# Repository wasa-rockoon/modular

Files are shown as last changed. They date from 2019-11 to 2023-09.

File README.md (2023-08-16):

# モジュラー電装

# バス

バスの物理規格は，2.54mmピッチのカードエッジコネクタとする．片面15ピンずつ．

CANを用いた通信プロトコルは [WCCP](https://github.com/wasa-rockoon/WCCP)を参照．

表
1. Vpp
2. Vcc 5V
3. Vdd 3.3V
4. VBAT 3V
5. GND
6. CAN Low
7. CAN High
8. GND
9. キー
10. JTMS, SWDIO
11. JTCK, SWCLK
12. JTDI
13. JTDO, TRACESWO
14. /JNTRST
15. /RESET
裏

16 ~ 23, 25 ~ 30. テスト用プローブ 1 ~ 8, 9 ~ 14

24. キー

## Vpp, Vcc, Vdd, GND

電源モジュールから供給される．バスからのVpp供給は小電流に限る．大電流が必要なモジュールには電源モジュールまたは外部から直接供給すること．

## CAN High, CAN Low

5V CANバス, Normal CAN 1Mbps

## SWCLK, SWDIO, RST

STM32書き込み・デバッグ用

# モジュール一覧

## ベース基板

6個のモジュールを搭載できるベース基板．
カードエッジコネクタのうち1つを書き込み・デバッグ用とする．

- カードエッジコネクタ x6
- CANバスコネクタ x2
- STLink 書き込み・デバッグ用コネクタ x1
- テスト用カードエッジ

### CANバスコネクタ

ベース基板に取り付けないモジュールとの中距離接続に用いる．

1. Vpp
2. CAN Low
3. CAN High
4. GND

Vcc, Vddはモジュール側で自給する．

接続しない場合は，CAN Low と CAN High との間に終端抵抗（120 Ω）を必ず接続すること．

## Battery Power

- 5Vおよび3.3Vの電源を供給
- 各系統の電圧および電流を測定

### 接続

- 電源供給（6V~18V）：XH (1: V+, 2: GND)

### インターフェース

- 主電源スイッチ
- バックアップ電源スイッチ

### 出力パケット

#### B （Battery）

| Type | Data | Description |
| --- | --- | --- |
| P | float16 | 供給電源電圧 [V] |
| C | float16 | 5V系電圧 [V] |
| D | float16 | 3.3V系電圧 [V] |
| c | float16 | 5V系電圧 [A] |
| d | float16 | 3.3V系電流 [A] |

## Battery Power V2

- 5Vおよび3.3Vの電源を供給
- 各系統の電圧および電流を測定
- 外部に5Vまたは3.3Vの電源を供給
- バッテリー温度を測定し，ヒーターを駆動

### 接続

- 電源供給1（6V~18V）：XH (1: V+, 2: GND)
- 電源供給2（6V~18V）：XH (1: V+, 2: GND)
- ヒーター：PH (1: Heater+, 2: GND, 3: temperature)
- 外部供給出力（5V or 3.3V）：PH (1: V+, 2: GND, 3: flight pin)
- 外部電源スイッチ：PH

### インターフェース

- 5V・3.3V系電源スイッチ（外部スイッチとどちらかがONならば供給）

### 出力パケット

#### B （Battery）

| Type | Data | Description |
| --- | --- | --- |
| P | float16 | 供給電源電圧 [V] |
| C | float16 | 5V系電圧 [V] |
| D | float16 | 3.3V系電圧 [V] |
| c | float16 | 5V系電圧 [A] |
| d | float16 | 3.3V系電流 [A] |

## Comm&Log

- LoRa（ES920LR）通信
- TWELITE 通信
- Micro SD カードにログを記録

### 接続

- LoRa アンテナ：U.FL
- TWELITE アンテナ：U.FL

### インターフェース

- Micro SD カードスロット

## LoRa

- LoRa（ES920LR）通信（2ch）

### 接続

- LoRa アンテナx2：U.FL

## Igniter Driver

- 発射条件を判定しイグナイタを駆動
- 供給電圧，電流，イグナイタ抵抗値を測定

### 接続

- イグナイタ用供給（6V~12V）：XH (1: V+, 2: GND)
- イグナイタ出力：XH (1: V+, 2: GND)

### インターフェース

- 警報ブザー

## Nav

- 9軸センサ（BMX055）
- 気圧センサ（BME280）
- GNSS

### 接続

- GPS パッシブアンテナ：U.FL
- UART （外部GPS用）：PH
- I2C （拡張用）：PH

## INS

- 9軸センサ（BNO055）
- 気圧センサ（BME280）
- GNSS (NEO-M9N-00B)

### 接続

- GPS アクティブアンテナ：U.FL
- サーミスタ：PH
- UART （拡張用）：PH
- I2C （拡張用）：PH

## RCS

- 電磁バルブ制御x4
- バルブ用電源（24V）供給
- 圧力計測（1MPaG）x2
- 推力計測x2
- 温度計測

### 接続

- バルブAB：PH (1: A+, 2: A-, 3: B+, 4: B-)
- バルブCD：PH (1: C+, 2: C-, 3: D+, 4: D-)
- ロードセルX：ZH (1: Vdd, 2: GND, 3: Signal+, 4: Signal-)
- ロードセルY：ZH (1: Vdd, 2: GND, 3: Signal+, 4: Signal-)
- 圧力センサ1：ZH (1: Vcc, 2: GND, 3: Signal)
- 圧力センサ2：ZH (1: Vcc, 2: GND, 3: Signal)
- サーミスタ：ZH

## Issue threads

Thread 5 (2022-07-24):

位置情報表示器

fujiy, 2022-07-24:
地上局で位置情報を表示するものが欲しい
2個あるといいかも

https://paper.dropbox.com/doc/--Bk29owoF~U5IUNhlMDIlKGDbAQ-byOXNlpulk8jaebLoAD3U

- [x] ブレッドボードモデル製作
- [x] プログラム製作
- [x] 本番用基板製作

Closed 2023-04-29.

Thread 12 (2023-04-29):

点火モジュール改良

fujiy, 2023-04-29:
基板作り直すなら
- MOSFETの定格増やす
- 電流測定回路間違ってたので修正する
- 温度センサ付けられるようにする

fujiy, 2023-07-29:
去年のモジュールを使うが，電流をコントロールするようにプログラムを改良する

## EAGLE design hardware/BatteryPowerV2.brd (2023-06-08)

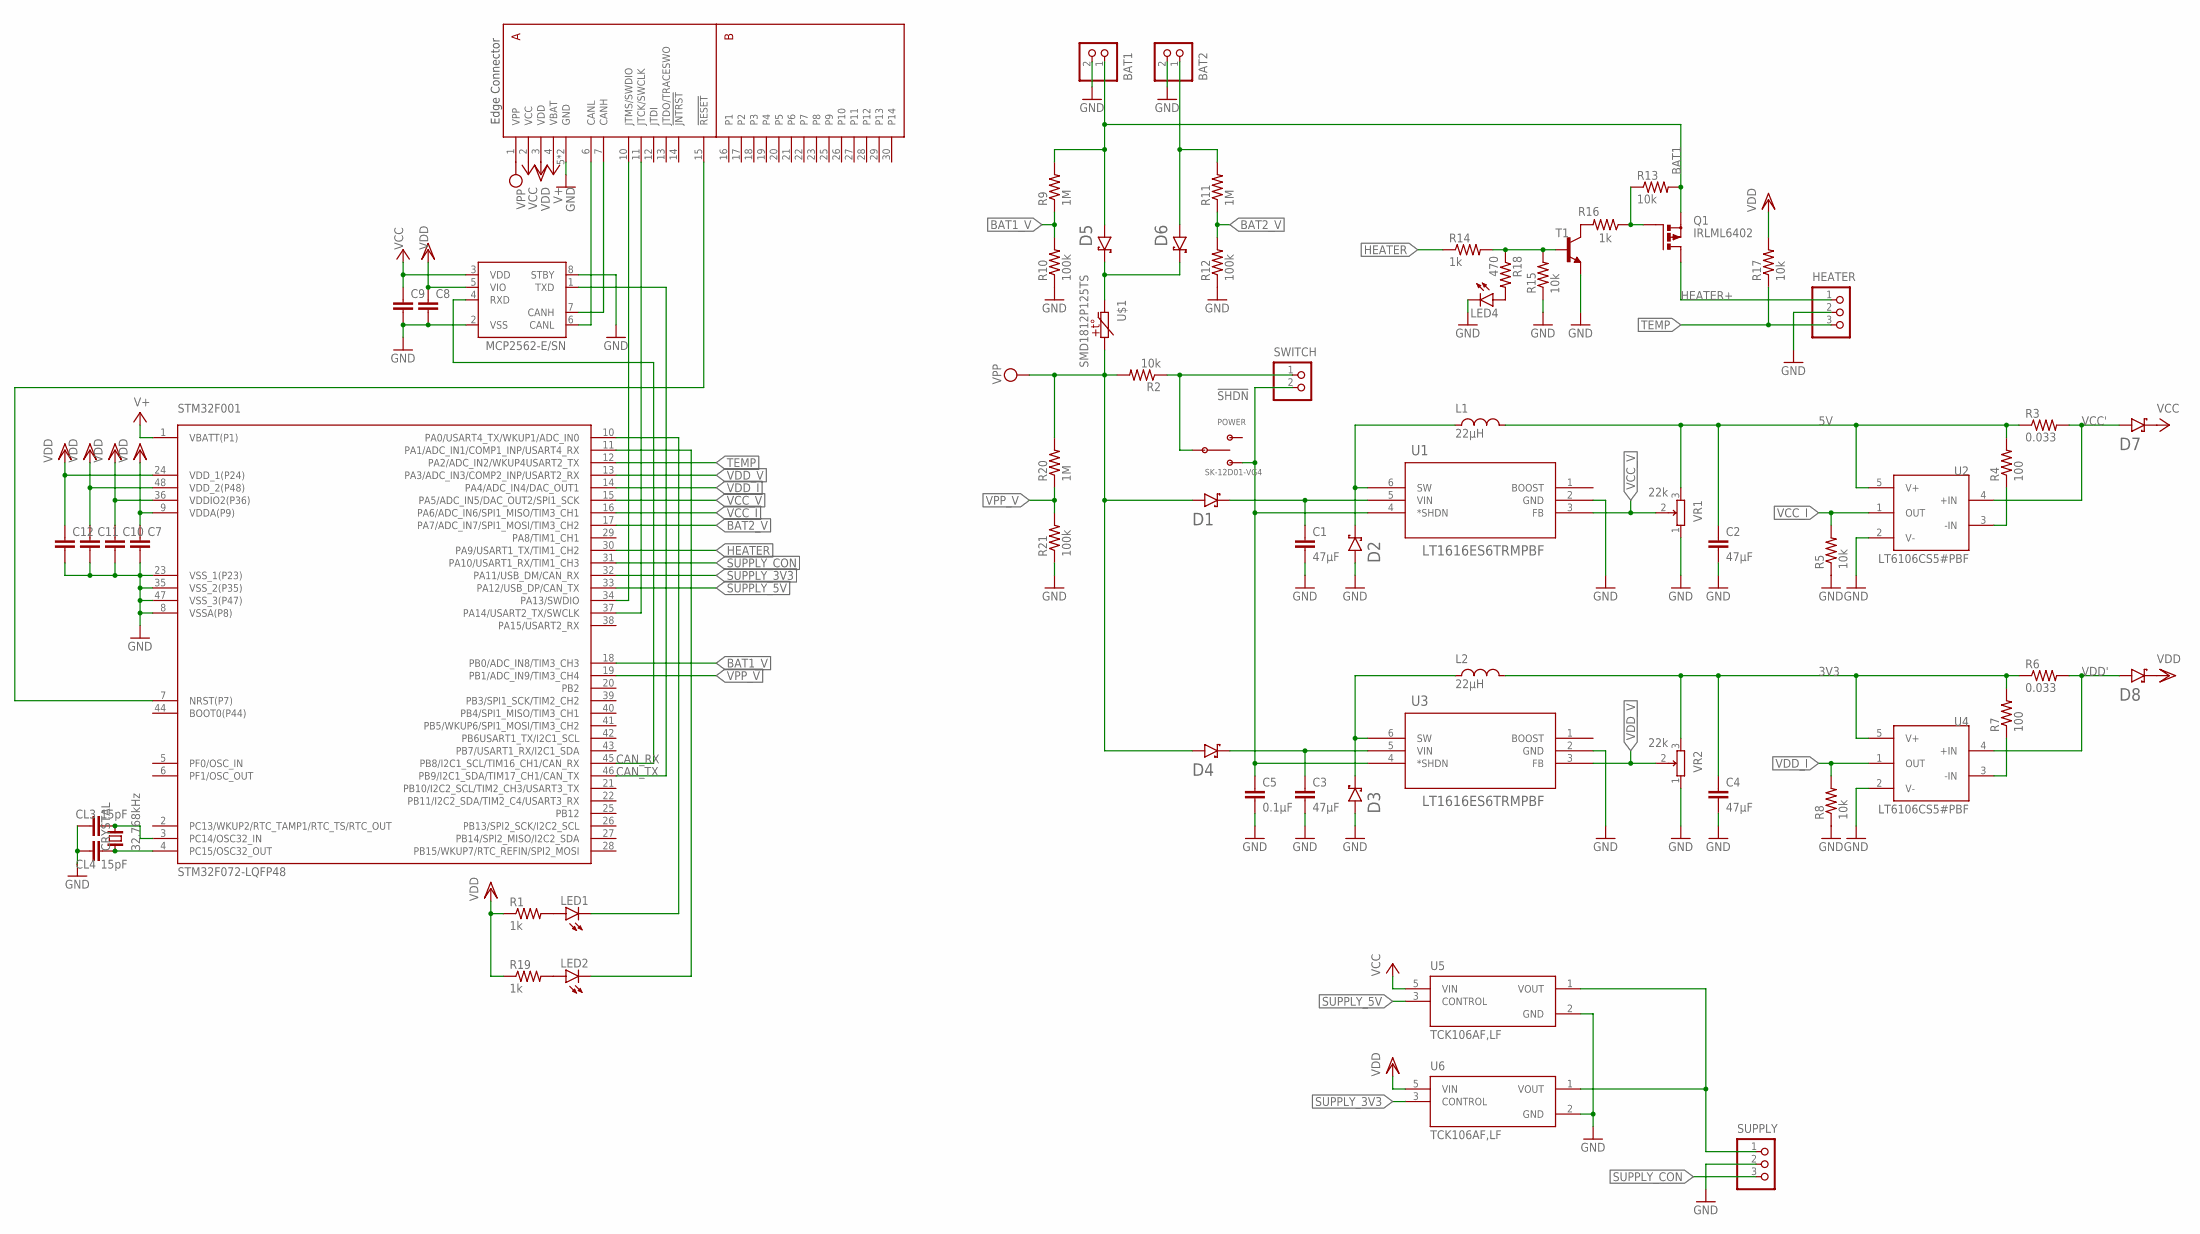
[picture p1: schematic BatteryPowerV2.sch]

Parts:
BAT1, BAT2: S2B-XH-A
C1, C2, C3, C4: 47µF; C0603
C5: 0.1µF; C0603
C7, C8, C9, C10, C11, C12: C-EUC0603K; C0603K
CL3, CL4: 15pF; C0603K
CRYSTAL: 32.768kHz; FC-255
D1, D2, D3, D4, D5, D6, D7, D8: CUHS20S30
HEATER: S3B-PH-K-S
L1, L2: 22µH; NR10050
LED1, LED2: LEDCHIP-LED0603; CHIP-LED0603
LED4: LEDCHIPLED_0603; CHIPLED_0603
MCP2562: MCP2562-E/SN; SOIC127P600X175-8N
POWER: SK-12D01-VG4
Q1: IRLML6402; SOT-23
R1, R14, R16, R19: 1k; R0603
R2, R5, R8, R13, R15, R17: 10k; R0603
R3, R6: 0.033; R0603
R4, R7: 100; R0603
R9, R11, R20: 1M; R0603
R10, R12, R21: 100k; R0603
R18: 470; R0603
STM32F001: STM32F072-LQFP48; LQFP48
SUPPLY: S3B-PH-K-S
SWITCH: S2B-PH-K-S
T1: -NPN-SOT23-EBC; SOT23-EBC
U1, U3: LT1616ES6TRMPBF; SOT-6_S
U2, U4: LT6106CS5#PBF; SOT95P280X100-5N_LT6106CS5#PBF
U5, U6: TCK106AF,LF; IC_TCK106AF,LF
U$1: SMD1812P125TS; SMD1812P
U$2: EDGE30
VR1, VR2: 22k; PVZ3A

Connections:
3V3: C4.1, L2.2, R6.1, R7.2, U4.5 (V+), VR2.3
5V: C2.1, L1.2, R3.1, R4.2, U2.5 (V+), VR1.3
!SHDN!: C5.1, POWER.B, SWITCH.2, U1.4 (*SHDN), U3.4 (*SHDN)
BAT1: BAT1.1, D5.A, Q1.P2 (S), R9.2, R13.2
BAT1_V: R9.1, R10.2, STM32F001.18 (PB0/ADC_IN8/TIM3_CH3)
BAT2: BAT2.1, D6.A, R11.2
BAT2_V: R11.1, R12.2, STM32F001.17 (PA7/ADC_IN7/SPI1_MOSI/TIM3_CH2)
CANH1: MCP2562.7 (CANH), U$2.7 (CANH)
CANL1: MCP2562.6 (CANL), U$2.6 (CANL)
CAN_RX: MCP2562.4 (RXD), STM32F001.45 (PB8/I2C1_SCL/TIM16_CH1/CAN_RX)
CAN_TX: MCP2562.1 (TXD), STM32F001.46 (PB9/I2C1_SDA/TIM17_CH1/CAN_TX)
GND: BAT1.2, BAT2.2, C1.2, C2.2, C3.2, C4.2, C5.2, C7.2, C8.2, C9.2, C10.2, C11.2, C12.2, CL3.1, CL4.1, D2.A, D3.A, HEATER.2, LED4.C, MCP2562.2 (VSS), MCP2562.8 (STBY), R5.1, R8.1, R10.1, R12.1, R15.1, R21.1, STM32F001.8 (VSSA(P8)), STM32F001.23 (VSS_1(P23)), STM32F001.35 (VSS_2(P35)), STM32F001.47 (VSS_3(P47)), SUPPLY.2, T1.E, U1.2 (GND), U2.2 (V-), U3.2 (GND), U4.2 (V-), U5.2 (GND), U6.2 (GND), U$2.5 (GND), U$2.8 (GND), VR1.1, VR2.1
HEATER: R14.1, STM32F001.30 (PA9/USART1_TX/TIM1_CH2)
HEATER+: HEATER.1, Q1.P3 (D)
unnamed: SUPPLY.1, U5.1 (VOUT), U6.1 (VOUT)
unnamed: R4.1, U2.3 (-IN)
unnamed: Q1.P1 (G), R13.1, R16.1
unnamed: LED2.C, STM32F001.11 (PA1/ADC_IN1/COMP1_INP/USART4_RX)
unnamed: R7.1, U4.3 (-IN)
unnamed: POWER.C, R2.1, SWITCH.1
unnamed: LED2.A, R19.2
unnamed: R14.2, R15.2, R18.1, T1.B
unnamed: R16.2, T1.C
unnamed: LED4.A, R18.2
unnamed: CL4.2, CRYSTAL.1, STM32F001.4 (PC15/OSC32_OUT)
unnamed: CL3.2, CRYSTAL.2, STM32F001.3 (PC14/OSC32_IN)
unnamed: LED1.C, STM32F001.10 (PA0/USART4_TX/WKUP1/ADC_IN0)
unnamed: LED1.A, R1.2
NRST1: STM32F001.7 (NRST(P7)), U$2.15 (!RESET!)
SUPPLY_3V3: STM32F001.32 (PA11/USB_DM/CAN_RX), U6.3 (CONTROL)
SUPPLY_5V: STM32F001.33 (PA12/USB_DP/CAN_TX), U5.3 (CONTROL)
SUPPLY_CON: STM32F001.31 (PA10/USART1_RX/TIM1_CH3), SUPPLY.3
SWCLK1: STM32F001.37 (PA14/USART2_TX/SWCLK), U$2.11 (JTCK/SWCLK)
SWDIO1: STM32F001.34 (PA13/SWDIO), U$2.10 (JTMS/SWDIO)
TEMP: HEATER.3, R17.1, STM32F001.12 (PA2/ADC_IN2/WKUP4USART2_TX)
VBAT: STM32F001.1 (VBATT(P1)), U$2.4 (VBAT)
VCC: C9.1, D7.C, MCP2562.3 (VDD), U5.5 (VIN), U$2.2 (VCC)
VCC': D7.A, R3.2, U2.4 (+IN)
VCC_I: R5.2, STM32F001.16 (PA6/ADC_IN6/SPI1_MISO/TIM3_CH1), U2.1 (OUT)
VCC_IN: C1.1, D1.C, U1.5 (VIN)
VCC_SW: D2.C, L1.1, U1.6 (SW)
VCC_V: STM32F001.15 (PA5/ADC_IN5/DAC_OUT2/SPI1_SCK), U1.3 (FB), VR1.2
VDD: C7.1, C8.1, C10.1, C11.1, C12.1, D8.C, MCP2562.5 (VIO), R1.1, R17.2, R19.1, STM32F001.9 (VDDA(P9)), STM32F001.24 (VDD_1(P24)), STM32F001.36 (VDDIO2(P36)), STM32F001.48 (VDD_2(P48)), U6.5 (VIN), U$2.3 (VDD)
VDD': D8.A, R6.2, U4.4 (+IN)
VDD_I: R8.2, STM32F001.14 (PA4/ADC_IN4/DAC_OUT1), U4.1 (OUT)
VDD_IN: C3.1, D4.C, U3.5 (VIN)
VDD_SW: D3.C, L2.1, U3.6 (SW)
VDD_V: STM32F001.13 (PA3/ADC_IN3/COMP2_INP/USART2_RX), U3.3 (FB), VR2.2
VPP: D1.A, D4.A, R2.2, R20.2, U$1.2, U$2.1 (VPP)
VPP_IN: D5.C, D6.C, U$1.1
VPP_V: R20.1, R21.2, STM32F001.19 (PB1/ADC_IN9/TIM3_CH4)

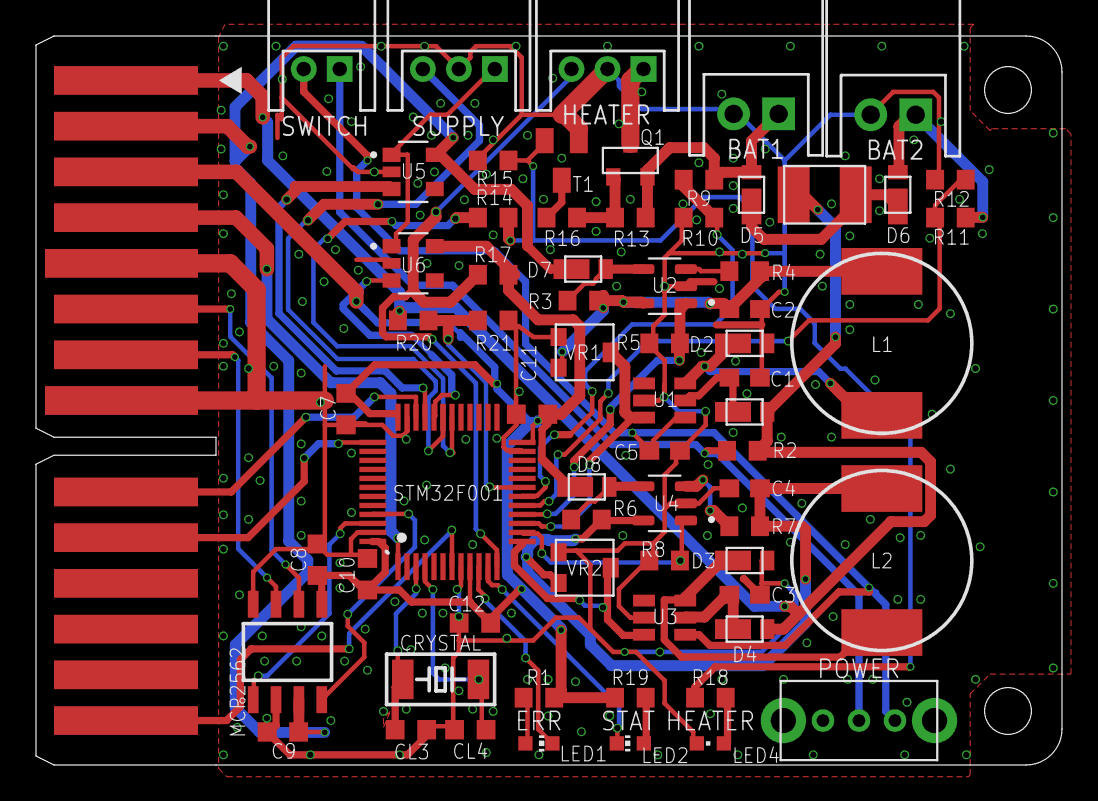
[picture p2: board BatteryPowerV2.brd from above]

Board: 2 copper layers, 57.0 x 40.5 mm, 68 parts (0 on the bottom side), 51 nets.

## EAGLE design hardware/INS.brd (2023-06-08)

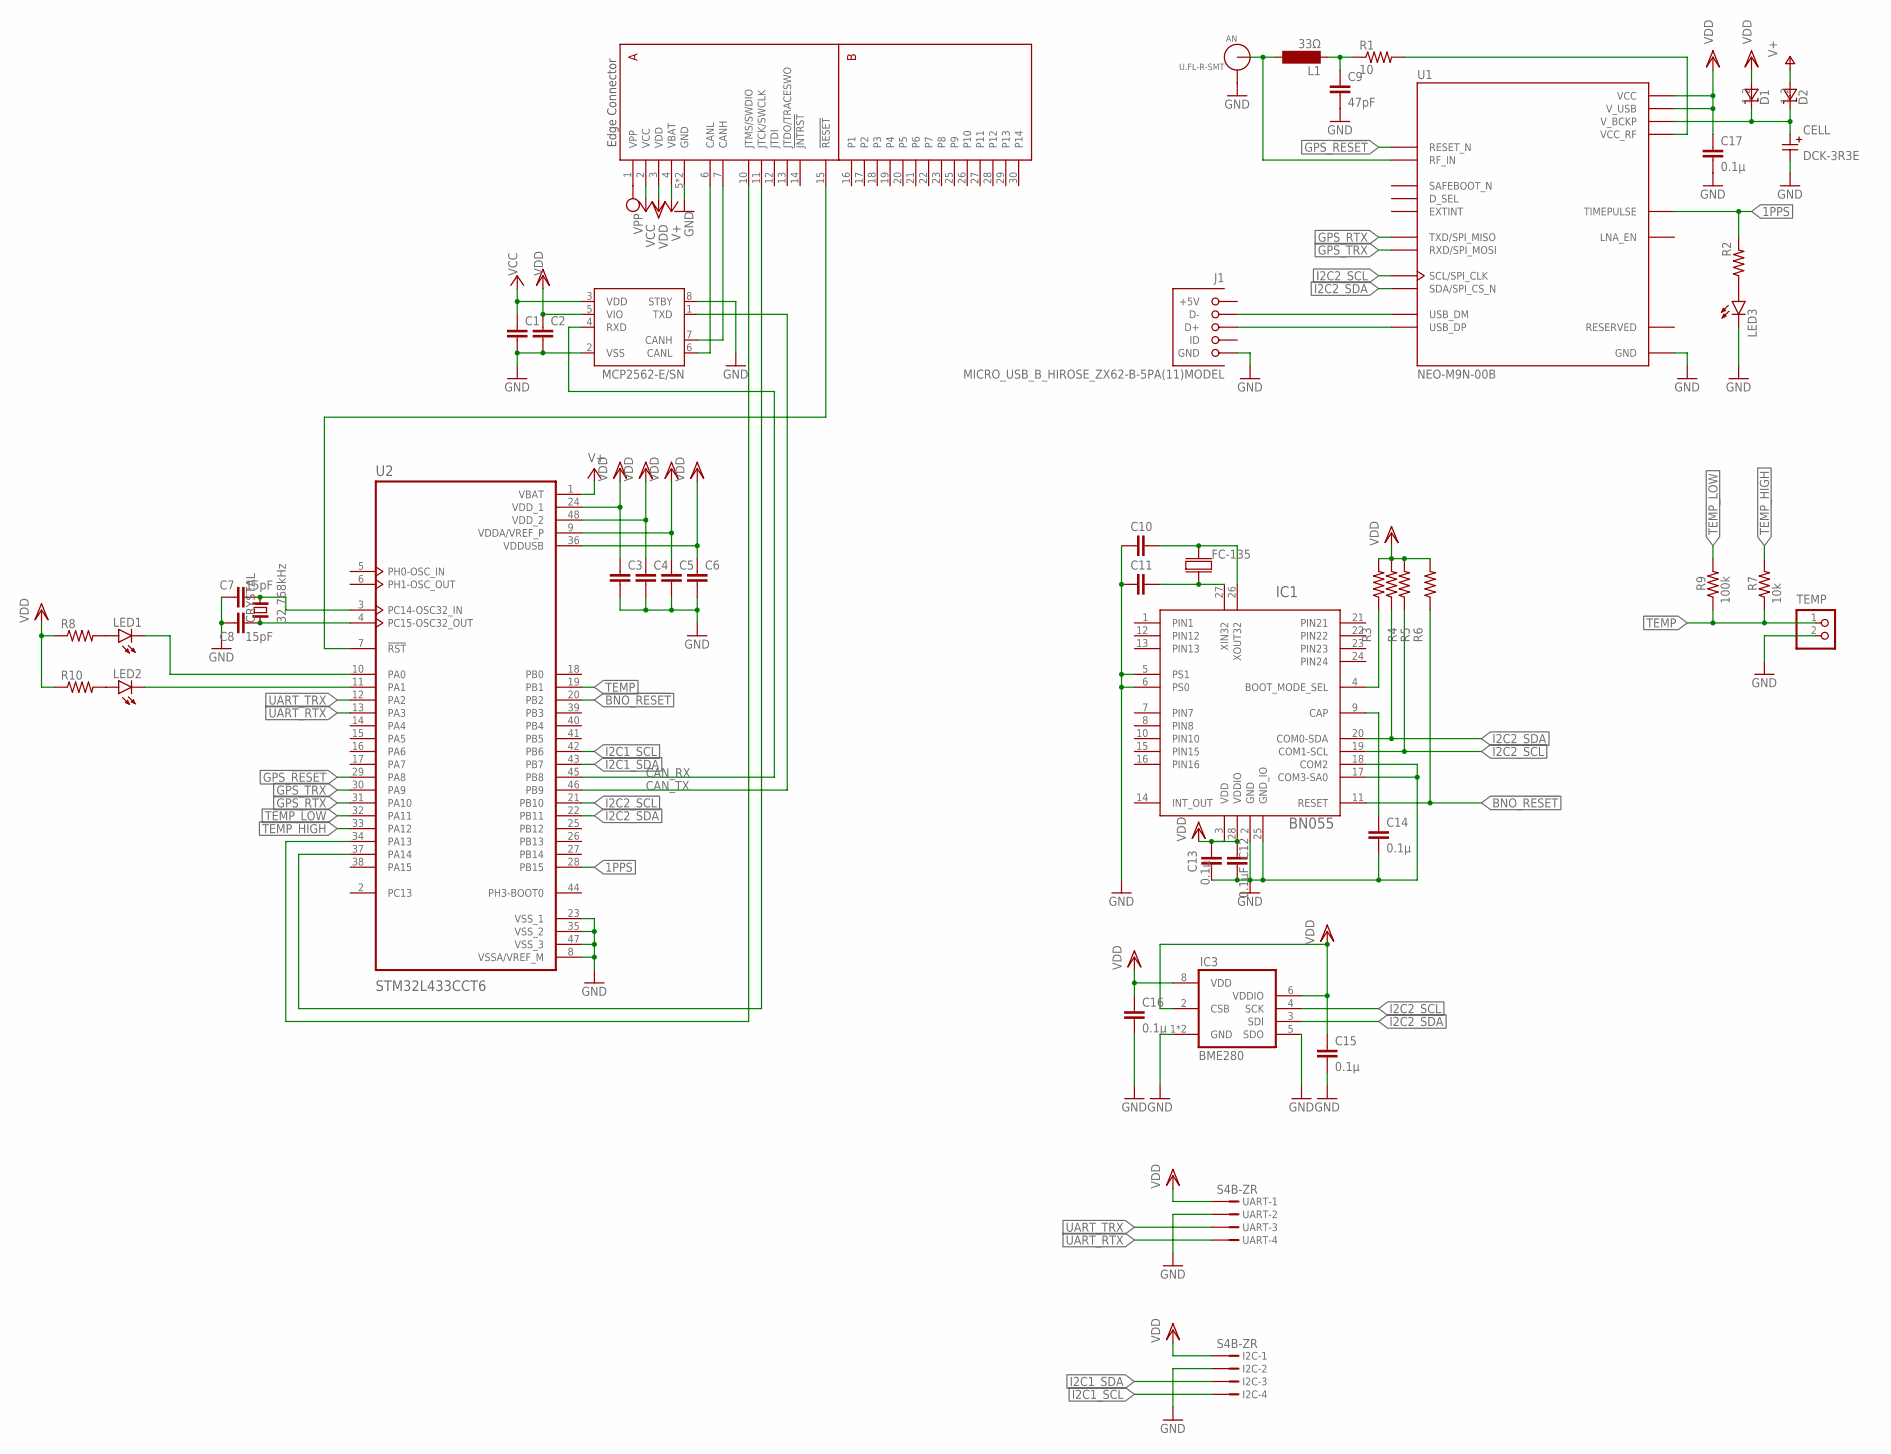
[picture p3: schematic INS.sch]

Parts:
AN: U.FL-R-SMT; U.FL_SMT
C1, C2, C3, C4, C5, C6: C-EUC0603K; C0603K
C7, C8: 15pF; C0603K
C9: 47pF; C0603
C10, C11: C-EUC0603; C0603
C12: 0.1µF; C0603
C13, C14, C15, C16, C17: 0.1µ; C0603
CELL: DCK-3R3E; DC,DCK
CRYSTAL: 32.768kHz; FC-255
D1, D2: RB521S-30TE61; SODFL1608X70N
FC-135: FC-135
I2C: S4B-ZR
IC1: BN055; LGA-28_3.80X5.20/0.5
IC3: BME280
J1: MICRO_USB_B_HIROSE_ZX62-B-5PA(11)MODEL; GHI-CONNECTORS_10118192-0001LF(MICRO-USB-B-AMPHENOL-FCI)
L1: 33Ω; SM-NE29
LED1, LED2, LED3: LEDCHIP-LED0603; CHIP-LED0603
MCP2562: MCP2562-E/SN; SOIC127P600X175-8N
R1: 10; R0603
R2, R3, R4, R5, R6, R8, R10: R-US_R0603; R0603
R7: 10k; R0603
R9: 100k; R0603
TEMP: S2B-PH-K-S
U1: NEO-M9N-00B; XCVR_NEO-M9N-00B
U2: STM32L433CCT6; QFP50P900X900X160-48N
U$2: EDGE30
UART: S4B-ZR

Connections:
1PPS: LED3.A, R2.1, R2.2, U1.3 (TIMEPULSE), U2.28 (PB15)
ANT: AN.SIG (ANT), L1.2, U1.11 (RF_IN)
BNO_!RESET!: IC1.11 (RESET), R6.1, U2.20 (PB2)
CANH1: MCP2562.7 (CANH), U$2.7 (CANH)
CANL1: MCP2562.6 (CANL), U$2.6 (CANL)
CAN_RX: MCP2562.4 (RXD), U2.45 (PB8)
CAN_TX: MCP2562.1 (TXD), U2.46 (PB9)
GND: AN.GND1, AN.GND2, C1.2, C2.2, C3.2, C4.2, C5.2, C6.2, C7.1, C8.1, C9.2, C10.1, C11.1, C12.2, C13.2, C14.2, C15.2, C16.2, C17.2, CELL.-, I2C.2, IC1.2 (GND), IC1.5 (PS1), IC1.6 (PS0), IC1.17 (COM3-SA0), IC1.18 (COM2), IC1.25 (GND_IO), IC3.1 (GND), IC3.5 (SDO), IC3.7 (GND), J1.CGND1 (GND), J1.CGND2 (GND), J1.CGND3 (GND), J1.CGND4 (GND), J1.CGND5 (GND), J1.CGND6 (GND), J1.GND, LED3.C, MCP2562.2 (VSS), MCP2562.8 (STBY), TEMP.2, U1.10 (GND), U1.12 (GND), U1.13 (GND), U1.24 (GND), U2.8 (VSSA/VREF_M), U2.23 (VSS_1), U2.35 (VSS_2), U2.47 (VSS_3), U$2.5 (GND), U$2.8 (GND), UART.2
GPS_!RESET!: U1.8 (RESET_N), U2.29 (PA8)
GPS_RTX: U1.20 (TXD/SPI_MISO), U2.31 (PA10)
GPS_TRX: U1.21 (RXD/SPI_MOSI), U2.30 (PA9)
I2C1_SCL: I2C.4, U2.42 (PB6)
I2C1_SDA: I2C.3, U2.43 (PB7)
I2C2_SCL: IC1.19 (COM1-SCL), IC3.4 (SCK), R5.1, U1.19 (SCL/SPI_CLK), U2.21 (PB10)
I2C2_SDA: IC1.20 (COM0-SDA), IC3.3 (SDI), R4.1, U1.18 (SDA/SPI_CS_N), U2.22 (PB11)
unnamed: R1.2, U1.9 (VCC_RF)
unnamed: U2.7 (!RST), U$2.15 (!RESET!)
unnamed: IC1.4 (BOOT_MODE_SEL), R3.1
unnamed: LED1.C, U2.10 (PA0)
unnamed: C9.1, L1.1, R1.1
unnamed: LED2.C, U2.11 (PA1)
unnamed: C14.1, IC1.9 (CAP)
unnamed: CELL.+, D1.1 (K), D2.1 (K), U1.22 (V_BCKP)
unnamed: LED2.A, R10.2
unnamed: C11.2, FC-135.P$2, IC1.27 (XIN32)
unnamed: C10.2, FC-135.P$1, IC1.26 (XOUT32)
unnamed: C8.2, CRYSTAL.1, U2.4 (PC15-OSC32_OUT)
unnamed: C7.2, CRYSTAL.2, U2.3 (PC14-OSC32_IN)
unnamed: LED1.A, R8.2
SWCLK1: U2.37 (PA14), U$2.11 (JTCK/SWCLK)
SWDIO1: U2.34 (PA13), U$2.10 (JTMS/SWDIO)
TEMP: R7.1, R9.1, TEMP.1, U2.19 (PB1)
TEMP_HIGH: R7.2, U2.33 (PA12)
TEMP_LOW: R9.2, U2.32 (PA11)
UART_RTX: U2.13 (PA3), UART.4
UART_TRX: U2.12 (PA2), UART.3
USB_D+: J1.D+, U1.6 (USB_DP)
USB_D-: J1.D-, U1.5 (USB_DM)
VBAT: D2.2 (A), U2.1 (VBAT), U$2.4 (VBAT)
VCC: C1.1, MCP2562.3 (VDD), U$2.2 (VCC)
VDD: C2.1, C3.1, C4.1, C5.1, C6.1, C12.1, C13.1, C15.1, C16.1, C17.1, D1.2 (A), I2C.1, IC1.3 (VDD), IC1.28 (VDDIO), IC3.2 (CSB), IC3.6 (VDDIO), IC3.8 (VDD), MCP2562.5 (VIO), R3.2, R4.2, R5.2, R6.2, R8.1, R10.1, U1.7 (V_USB), U1.23 (VCC), U2.9 (VDDA/VREF_P), U2.24 (VDD_1), U2.36 (VDDUSB), U2.48 (VDD_2), U$2.3 (VDD), UART.1
VPP: U$2.1 (VPP)

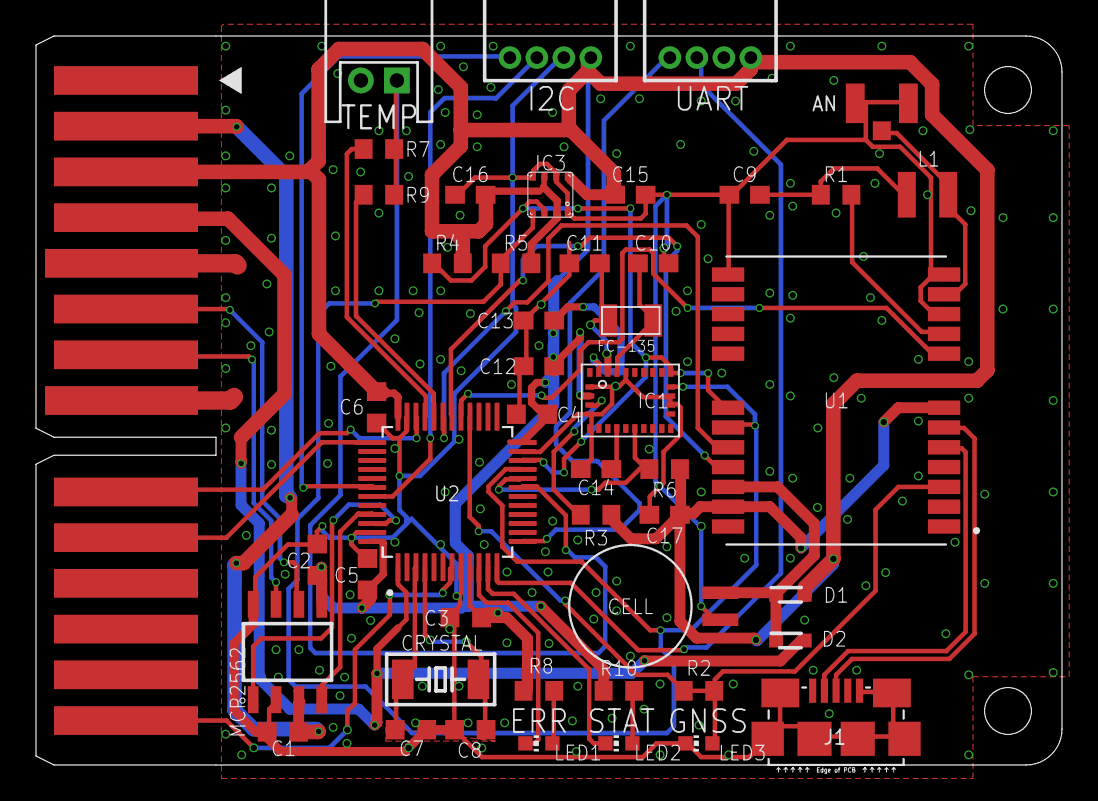
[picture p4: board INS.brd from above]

Board: 2 copper layers, 57.0 x 40.5 mm, 47 parts (0 on the bottom side), 41 nets.

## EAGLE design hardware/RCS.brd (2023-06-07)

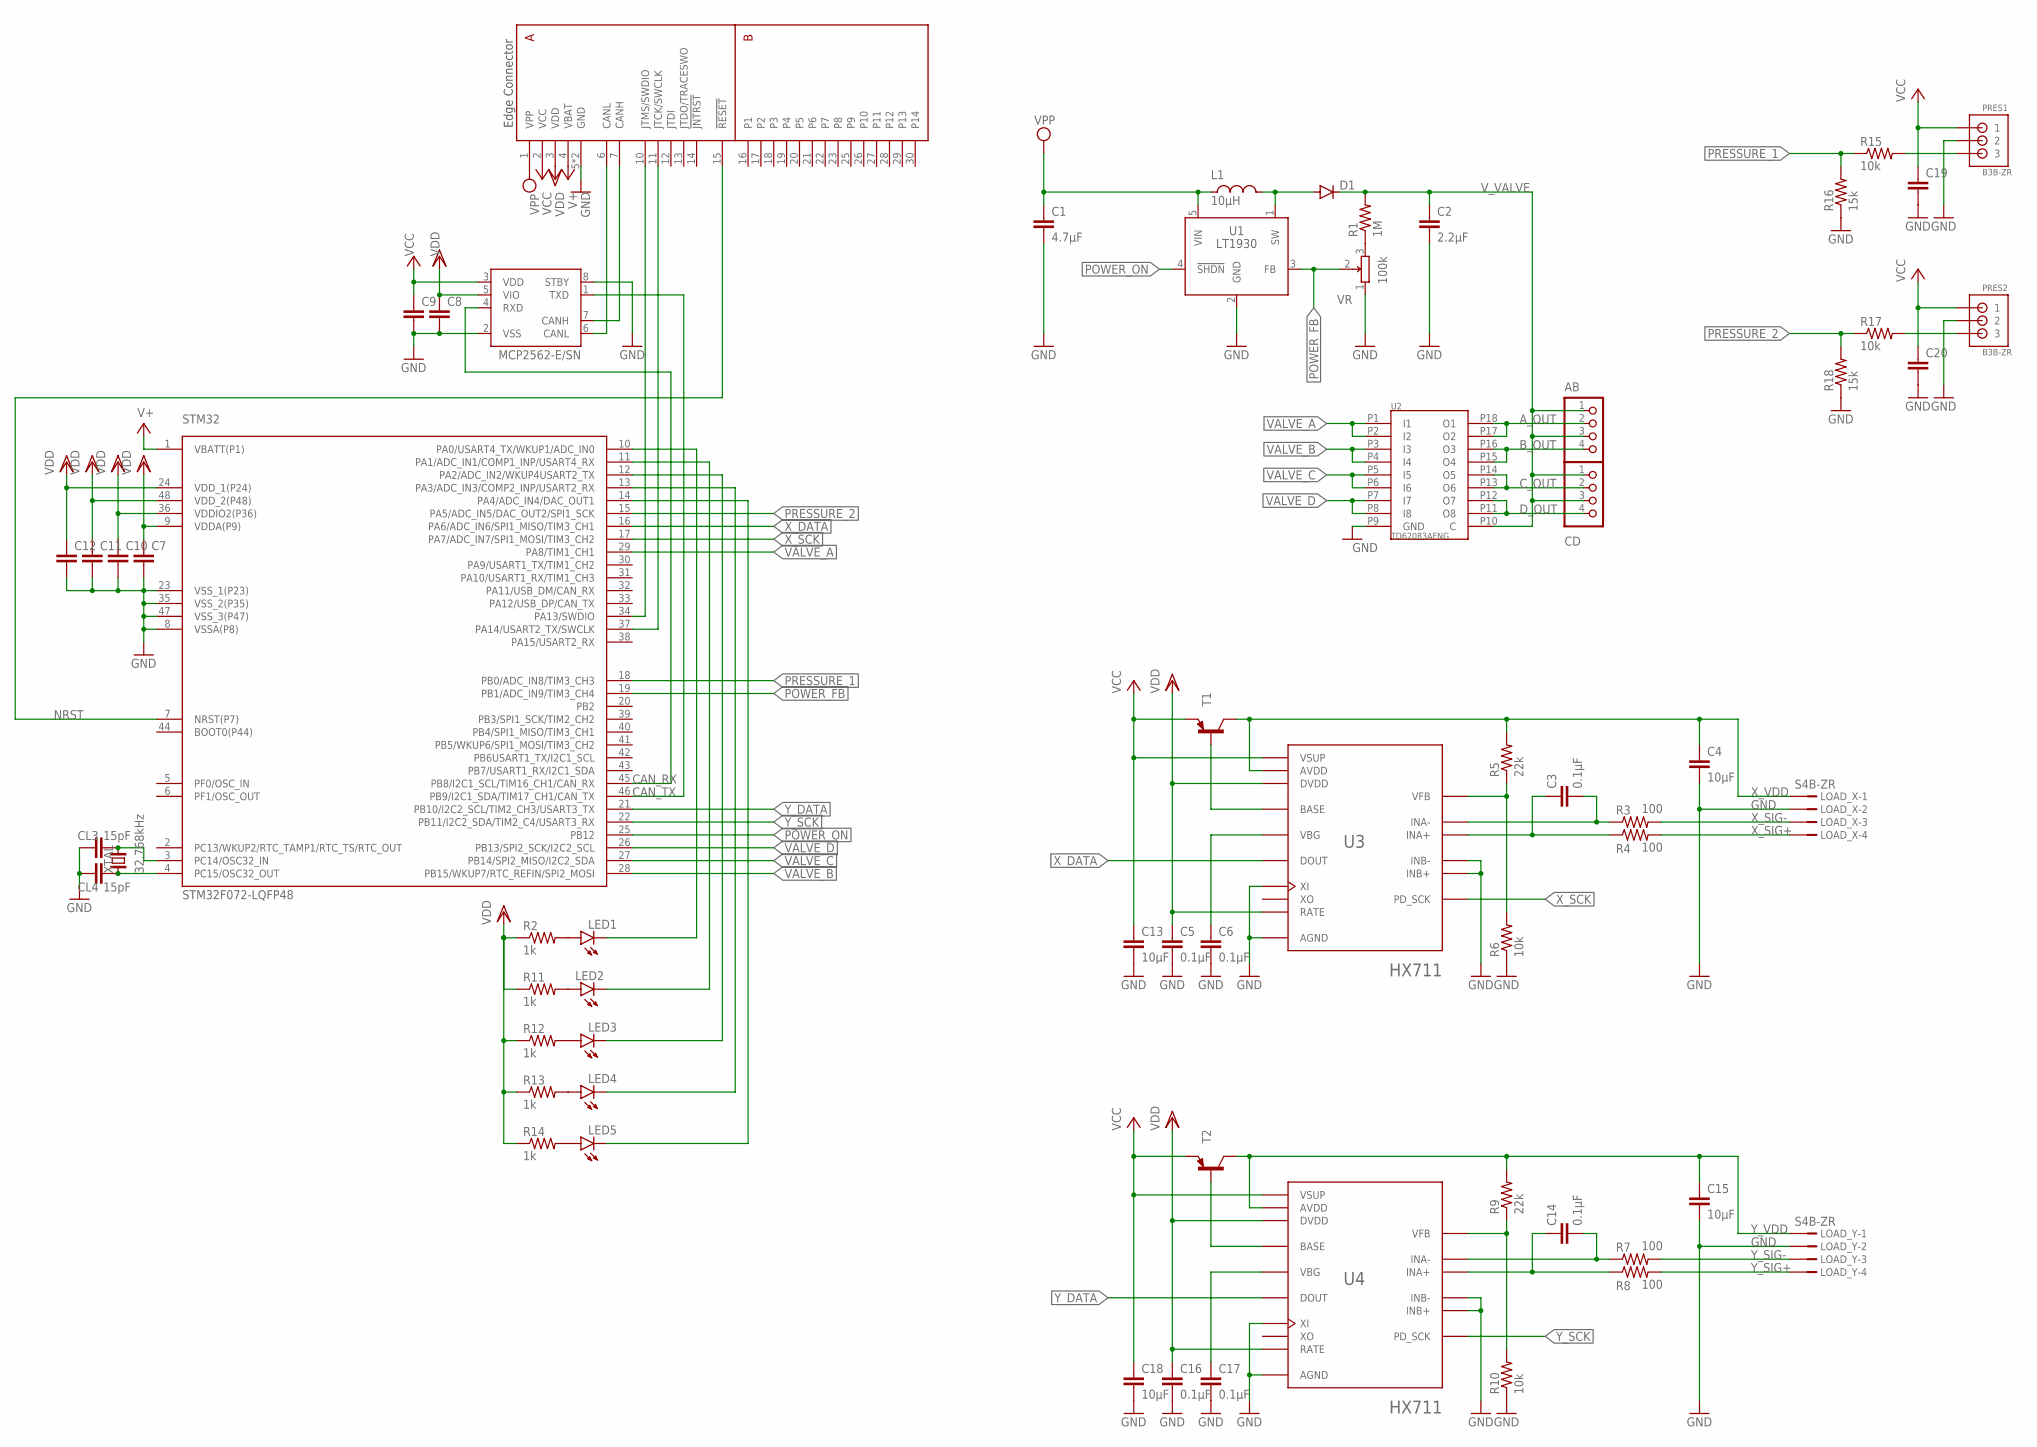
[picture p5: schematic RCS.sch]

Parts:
AB: S4B-PH-K-S
C1: 4.7µF; C0603
C2: 2.2µF; C0603
C3, C5, C6, C14, C16, C17: 0.1µF; C0603
C4, C13, C15, C18: 10µF; C0603
C7, C8, C9, C10, C11, C12: C-EUC0603K; C0603K
C19, C20: C-EUC0603; C0603
CD: S4B-PH-K-S
CL3, CL4: 15pF; C0603K
D1: DIODE-SOD123; SOD123
L1: 10µH; NR10050
LED1, LED2, LED3, LED4, LED5: LEDCHIP-LED0603; CHIP-LED0603
LOAD_X: S4B-ZR
LOAD_Y: S4B-ZR
MCP1: MCP2562-E/SN; SOIC127P600X175-8N
PRES1, PRES2: B3B-ZR
R1: 1M; R0603
R2, R11, R12, R13, R14: 1k; R0603
R3, R4, R7, R8: 100; R0603
R5, R9: 22k; R0603
R6, R10, R15, R17: 10k; R0603
R16, R18: 15k; R0603
STM32: STM32F072-LQFP48; LQFP48
T1, T2: BC857A-PNP-SOT23-BEC; SOT23-BEC
U1: LT1930; SOT95P240X110-5N
U2: TD62083AFNG; SSOP18-P-225-0.65
U3, U4: HX711; SOP127P600X180-16N
U$2: EDGE30
VR: 100k; PVZ3A
XTAL: 32.768kHz; FC-255

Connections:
A_OUT: AB.2, U2.P17 (O2), U2.P18 (O1)
B_OUT: AB.4, U2.P15 (O4), U2.P16 (O3)
CANH1: MCP1.7 (CANH), U$2.7 (CANH)
CANL1: MCP1.6 (CANL), U$2.6 (CANL)
CAN_RX: MCP1.4 (RXD), STM32.45 (PB8/I2C1_SCL/TIM16_CH1/CAN_RX)
CAN_TX: MCP1.1 (TXD), STM32.46 (PB9/I2C1_SDA/TIM17_CH1/CAN_TX)
C_OUT: CD.2, U2.P13 (O6), U2.P14 (O5)
D_OUT: CD.4, U2.P11 (O8), U2.P12 (O7)
GND: C1.2, C2.2, C4.2, C5.2, C6.2, C7.2, C8.2, C9.2, C10.2, C11.2, C12.2, C13.2, C15.2, C16.2, C17.2, C18.2, C19.2, C20.2, CL3.1, CL4.1, LOAD_X.2, LOAD_Y.2, MCP1.2 (VSS), MCP1.8 (STBY), PRES1.2, PRES2.2, R6.1, R10.1, R16.1, R18.1, STM32.8 (VSSA(P8)), STM32.23 (VSS_1(P23)), STM32.35 (VSS_2(P35)), STM32.47 (VSS_3(P47)), U1.2 (GND), U2.P9 (GND), U3.5 (AGND), U3.9 (INB-), U3.10 (INB+), U3.14 (XI), U4.5 (AGND), U4.9 (INB-), U4.10 (INB+), U4.14 (XI), U$2.5 (GND), U$2.8 (GND), VR.1
unnamed: R1.1, VR.3
unnamed: D1.A, L1.2, U1.1 (SW)
unnamed: C3.2, R3.1, U3.7 (INA-)
unnamed: C3.1, R4.1, U3.8 (INA+)
unnamed: R5.1, R6.2, U3.4 (VFB)
unnamed: T1.B, U3.2 (BASE)
unnamed: C6.1, U3.6 (VBG)
unnamed: PRES2.3, R17.2
unnamed: C14.2, R7.1, U4.7 (INA-)
unnamed: C14.1, R8.1, U4.8 (INA+)
unnamed: T2.B, U4.2 (BASE)
unnamed: C17.1, U4.6 (VBG)
unnamed: R9.1, R10.2, U4.4 (VFB)
unnamed: PRES1.3, R15.2
unnamed: LED3.C, STM32.12 (PA2/ADC_IN2/WKUP4USART2_TX)
unnamed: LED3.A, R12.2
unnamed: LED4.C, STM32.13 (PA3/ADC_IN3/COMP2_INP/USART2_RX)
unnamed: LED4.A, R13.2
unnamed: LED5.C, STM32.14 (PA4/ADC_IN4/DAC_OUT1)
unnamed: LED5.A, R14.2
unnamed: CL3.2, STM32.3 (PC14/OSC32_IN), XTAL.2
unnamed: LED2.C, STM32.11 (PA1/ADC_IN1/COMP1_INP/USART4_RX)
unnamed: LED2.A, R11.2
unnamed: LED1.C, STM32.10 (PA0/USART4_TX/WKUP1/ADC_IN0)
unnamed: CL4.2, STM32.4 (PC15/OSC32_OUT), XTAL.1
unnamed: LED1.A, R2.2
NRST: STM32.7 (NRST(P7)), U$2.15 (!RESET!)
POWER_FB: STM32.19 (PB1/ADC_IN9/TIM3_CH4), U1.3 (FB), VR.2
POWER_ON: STM32.25 (PB12), U1.4 (!SHDN!)
PRESSURE_1: R15.1, R16.2, STM32.18 (PB0/ADC_IN8/TIM3_CH3)
PRESSURE_2: R17.1, R18.2, STM32.15 (PA5/ADC_IN5/DAC_OUT2/SPI1_SCK)
SWCLK1: STM32.37 (PA14/USART2_TX/SWCLK), U$2.11 (JTCK/SWCLK)
SWDIO1: STM32.34 (PA13/SWDIO), U$2.10 (JTMS/SWDIO)
V+: STM32.1 (VBATT(P1))
VALVE_A: STM32.29 (PA8/TIM1_CH1), U2.P1 (I1), U2.P2 (I2)
VALVE_B: STM32.28 (PB15/WKUP7/RTC_REFIN/SPI2_MOSI), U2.P3 (I3), U2.P4 (I4)
VALVE_C: STM32.27 (PB14/SPI2_MISO/I2C2_SDA), U2.P5 (I5), U2.P6 (I6)
VALVE_D: STM32.26 (PB13/SPI2_SCK/I2C2_SCL), U2.P7 (I7), U2.P8 (I8)
VBAT: U$2.4 (VBAT)
VCC: C9.1, C13.1, C18.1, C19.1, C20.1, MCP1.3 (VDD), PRES1.1, PRES2.1, T1.E, T2.E, U3.1 (VSUP), U4.1 (VSUP), U$2.2 (VCC)
VDD: C5.1, C7.1, C8.1, C10.1, C11.1, C12.1, C16.1, MCP1.5 (VIO), R2.1, R11.1, R12.1, R13.1, R14.1, STM32.9 (VDDA(P9)), STM32.24 (VDD_1(P24)), STM32.36 (VDDIO2(P36)), STM32.48 (VDD_2(P48)), U3.15 (RATE), U3.16 (DVDD), U4.15 (RATE), U4.16 (DVDD), U$2.3 (VDD)
VPP: C1.1, L1.1, U1.5 (VIN), U$2.1 (VPP)
V_VALVE: AB.1, AB.3, C2.1, CD.1, CD.3, D1.C, R1.2, U2.P10 (C)
X_DATA: STM32.16 (PA6/ADC_IN6/SPI1_MISO/TIM3_CH1), U3.12 (DOUT)
X_SCK: STM32.17 (PA7/ADC_IN7/SPI1_MOSI/TIM3_CH2), U3.11 (PD_SCK)
X_SIG+: LOAD_X.4, R4.2
X_SIG-: LOAD_X.3, R3.2
X_VDD: C4.1, LOAD_X.1, R5.2, T1.C, U3.3 (AVDD)
Y_DATA: STM32.21 (PB10/I2C2_SCL/TIM2_CH3/USART3_TX), U4.12 (DOUT)
Y_SCK: STM32.22 (PB11/I2C2_SDA/TIM2_C4/USART3_RX), U4.11 (PD_SCK)
Y_SIG+: LOAD_Y.4, R8.2
Y_SIG-: LOAD_Y.3, R7.2
Y_VDD: C15.1, LOAD_Y.1, R9.2, T2.C, U4.3 (AVDD)

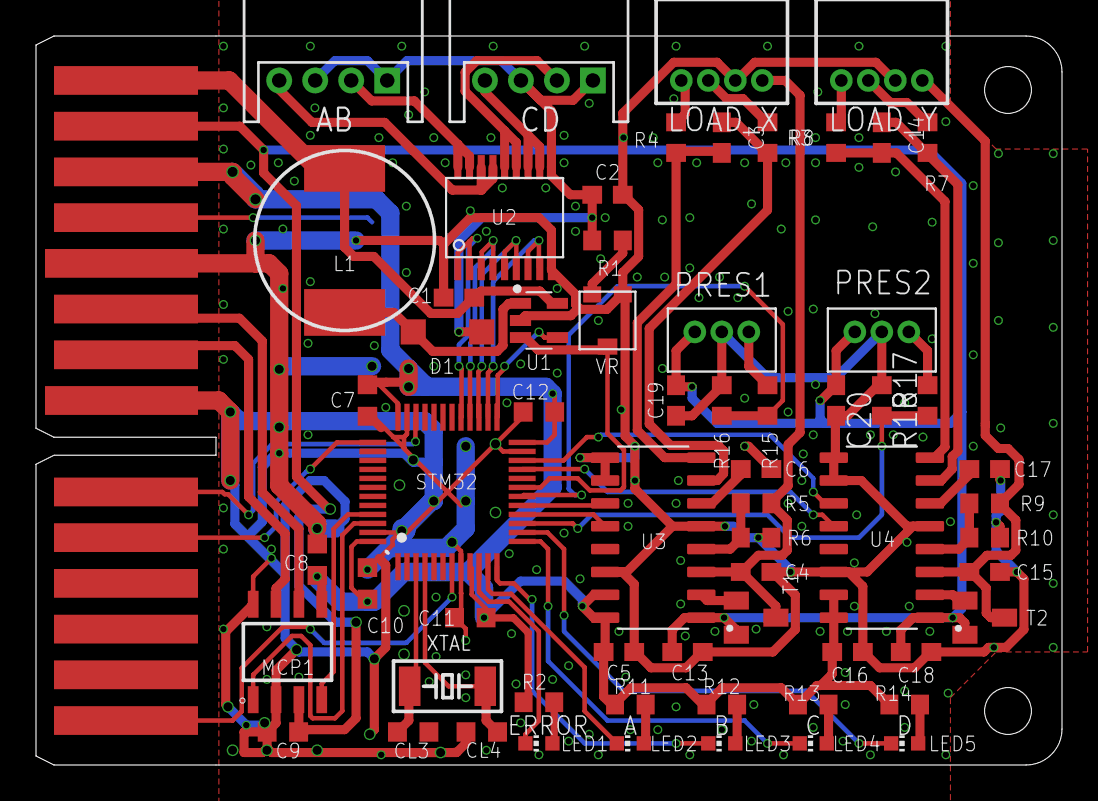
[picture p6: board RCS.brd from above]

Board: 2 copper layers, 57.0 x 40.5 mm, 64 parts (0 on the bottom side), 60 nets.

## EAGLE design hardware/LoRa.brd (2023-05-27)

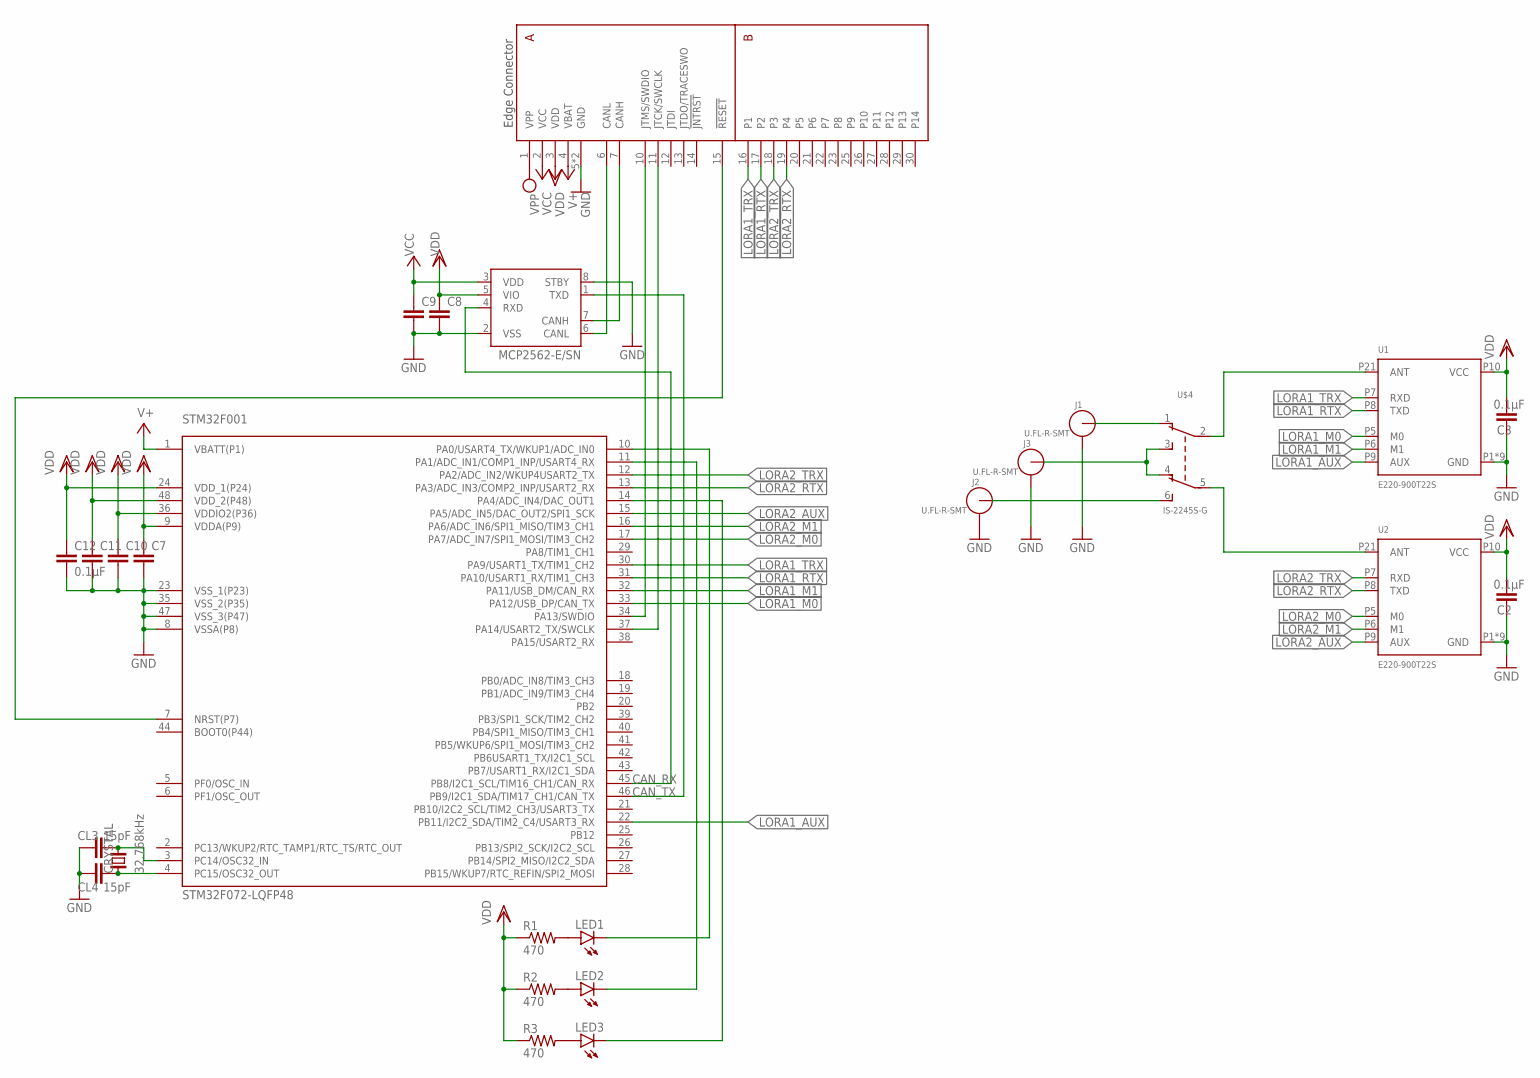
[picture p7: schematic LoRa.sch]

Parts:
C2, C3, C12: 0.1µF; C0603K
C7, C8, C9, C10, C11: C-EUC0603K; C0603K
CL3, CL4: 15pF; C0603K
CRYSTAL: 32.768kHz; FC-255
J1, J2, J3: U.FL-R-SMT; U.FL_SMT
LED1, LED2, LED3: LEDCHIP-LED0603; CHIP-LED0603
MCP1: MCP2562-E/SN; SOIC127P600X175-8N
R1, R2, R3: 470; R0603
STM32F001: STM32F072-LQFP48; LQFP48
U1, U2: E220-900T22S
U$2: EDGE30
U$4: IS-2245S-G

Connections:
CANH1: MCP1.7 (CANH), U$2.7 (CANH)
CANL1: MCP1.6 (CANL), U$2.6 (CANL)
CAN_RX: MCP1.4 (RXD), STM32F001.45 (PB8/I2C1_SCL/TIM16_CH1/CAN_RX)
CAN_TX: MCP1.1 (TXD), STM32F001.46 (PB9/I2C1_SDA/TIM17_CH1/CAN_TX)
GND: C2.1, C3.1, C7.2, C8.2, C9.2, C10.2, C11.2, C12.2, CL3.1, CL4.1, J1.GND1, J1.GND2, J2.GND1, J2.GND2, J3.GND1, J3.GND2, MCP1.2 (VSS), MCP1.8 (STBY), STM32F001.8 (VSSA(P8)), STM32F001.23 (VSS_1(P23)), STM32F001.35 (VSS_2(P35)), STM32F001.47 (VSS_3(P47)), U1.P1 (GND), U1.P2 (GND), U1.P3 (GND), U1.P4 (GND), U1.P11 (GND), U1.P13 (GND), U1.P19 (GND), U1.P20 (GND), U1.P22 (GND), U2.P1 (GND), U2.P2 (GND), U2.P3 (GND), U2.P4 (GND), U2.P11 (GND), U2.P13 (GND), U2.P19 (GND), U2.P20 (GND), U2.P22 (GND), U$2.5 (GND), U$2.8 (GND)
LORA1_AUX: STM32F001.22 (PB11/I2C2_SDA/TIM2_C4/USART3_RX), U1.P9 (AUX)
LORA1_M0: STM32F001.33 (PA12/USB_DP/CAN_TX), U1.P5 (M0)
LORA1_M1: STM32F001.32 (PA11/USB_DM/CAN_RX), U1.P6 (M1)
LORA1_RTX: STM32F001.31 (PA10/USART1_RX/TIM1_CH3), U1.P8 (TXD), U$2.17 (P2)
LORA1_TRX: STM32F001.30 (PA9/USART1_TX/TIM1_CH2), U1.P7 (RXD), U$2.16 (P1)
LORA2_AUX: STM32F001.15 (PA5/ADC_IN5/DAC_OUT2/SPI1_SCK), U2.P9 (AUX)
LORA2_M0: STM32F001.17 (PA7/ADC_IN7/SPI1_MOSI/TIM3_CH2), U2.P5 (M0)
LORA2_M1: STM32F001.16 (PA6/ADC_IN6/SPI1_MISO/TIM3_CH1), U2.P6 (M1)
LORA2_RTX: STM32F001.13 (PA3/ADC_IN3/COMP2_INP/USART2_RX), U2.P8 (TXD), U$2.19 (P4)
LORA2_TRX: STM32F001.12 (PA2/ADC_IN2/WKUP4USART2_TX), U2.P7 (RXD), U$2.18 (P3)
unnamed: U1.P21 (ANT), U$4.2
unnamed: U2.P21 (ANT), U$4.5
unnamed: LED2.A, R2.2
unnamed: J1.SIG (ANT), U$4.1
unnamed: LED3.C, STM32F001.14 (PA4/ADC_IN4/DAC_OUT1)
unnamed: J2.SIG (ANT), U$4.6
unnamed: J3.SIG (ANT), U$4.3, U$4.4
unnamed: LED3.A, R3.2
unnamed: LED1.C, STM32F001.10 (PA0/USART4_TX/WKUP1/ADC_IN0)
unnamed: CL4.2, CRYSTAL.1, STM32F001.4 (PC15/OSC32_OUT)
unnamed: CL3.2, CRYSTAL.2, STM32F001.3 (PC14/OSC32_IN)
unnamed: LED2.C, STM32F001.11 (PA1/ADC_IN1/COMP1_INP/USART4_RX)
unnamed: LED1.A, R1.2
NRST1: STM32F001.7 (NRST(P7)), U$2.15 (!RESET!)
SWCLK1: STM32F001.37 (PA14/USART2_TX/SWCLK), U$2.11 (JTCK/SWCLK)
SWDIO1: STM32F001.34 (PA13/SWDIO), U$2.10 (JTMS/SWDIO)
VBAT: STM32F001.1 (VBATT(P1)), U$2.4 (VBAT)
VCC: C9.1, MCP1.3 (VDD), U$2.2 (VCC)
VDD: C2.2, C3.2, C7.1, C8.1, C10.1, C11.1, C12.1, MCP1.5 (VIO), R1.1, R2.1, R3.1, STM32F001.9 (VDDA(P9)), STM32F001.24 (VDD_1(P24)), STM32F001.36 (VDDIO2(P36)), STM32F001.48 (VDD_2(P48)), U1.P10 (VCC), U2.P10 (VCC), U$2.3 (VDD)
VPP: U$2.1 (VPP)

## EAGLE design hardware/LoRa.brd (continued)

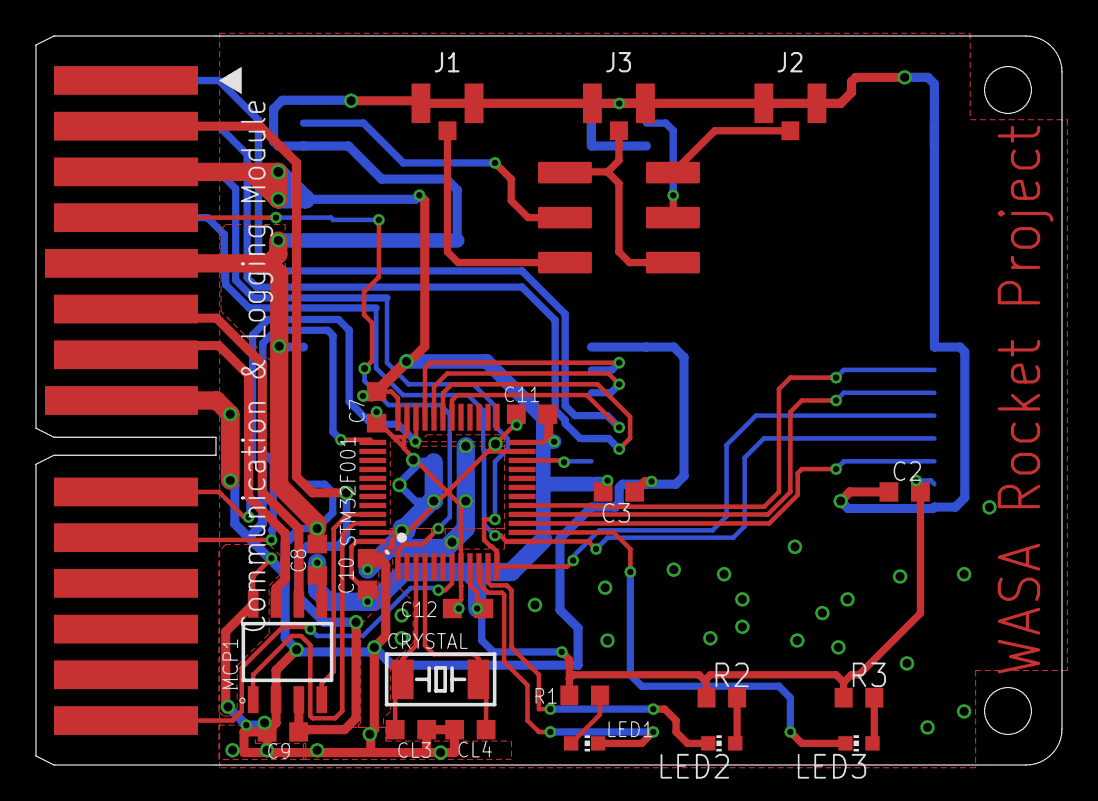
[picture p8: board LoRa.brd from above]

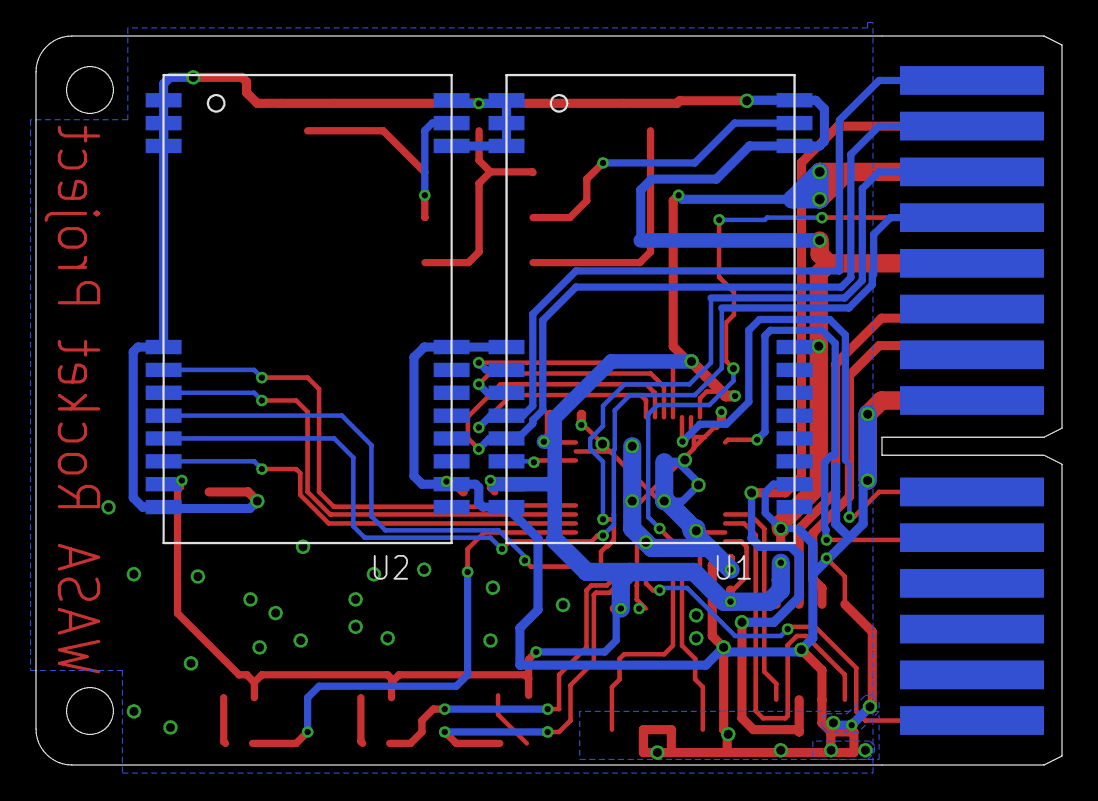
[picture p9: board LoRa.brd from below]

Board: 2 copper layers, 57.0 x 40.5 mm, 26 parts (2 on the bottom side), 34 nets.

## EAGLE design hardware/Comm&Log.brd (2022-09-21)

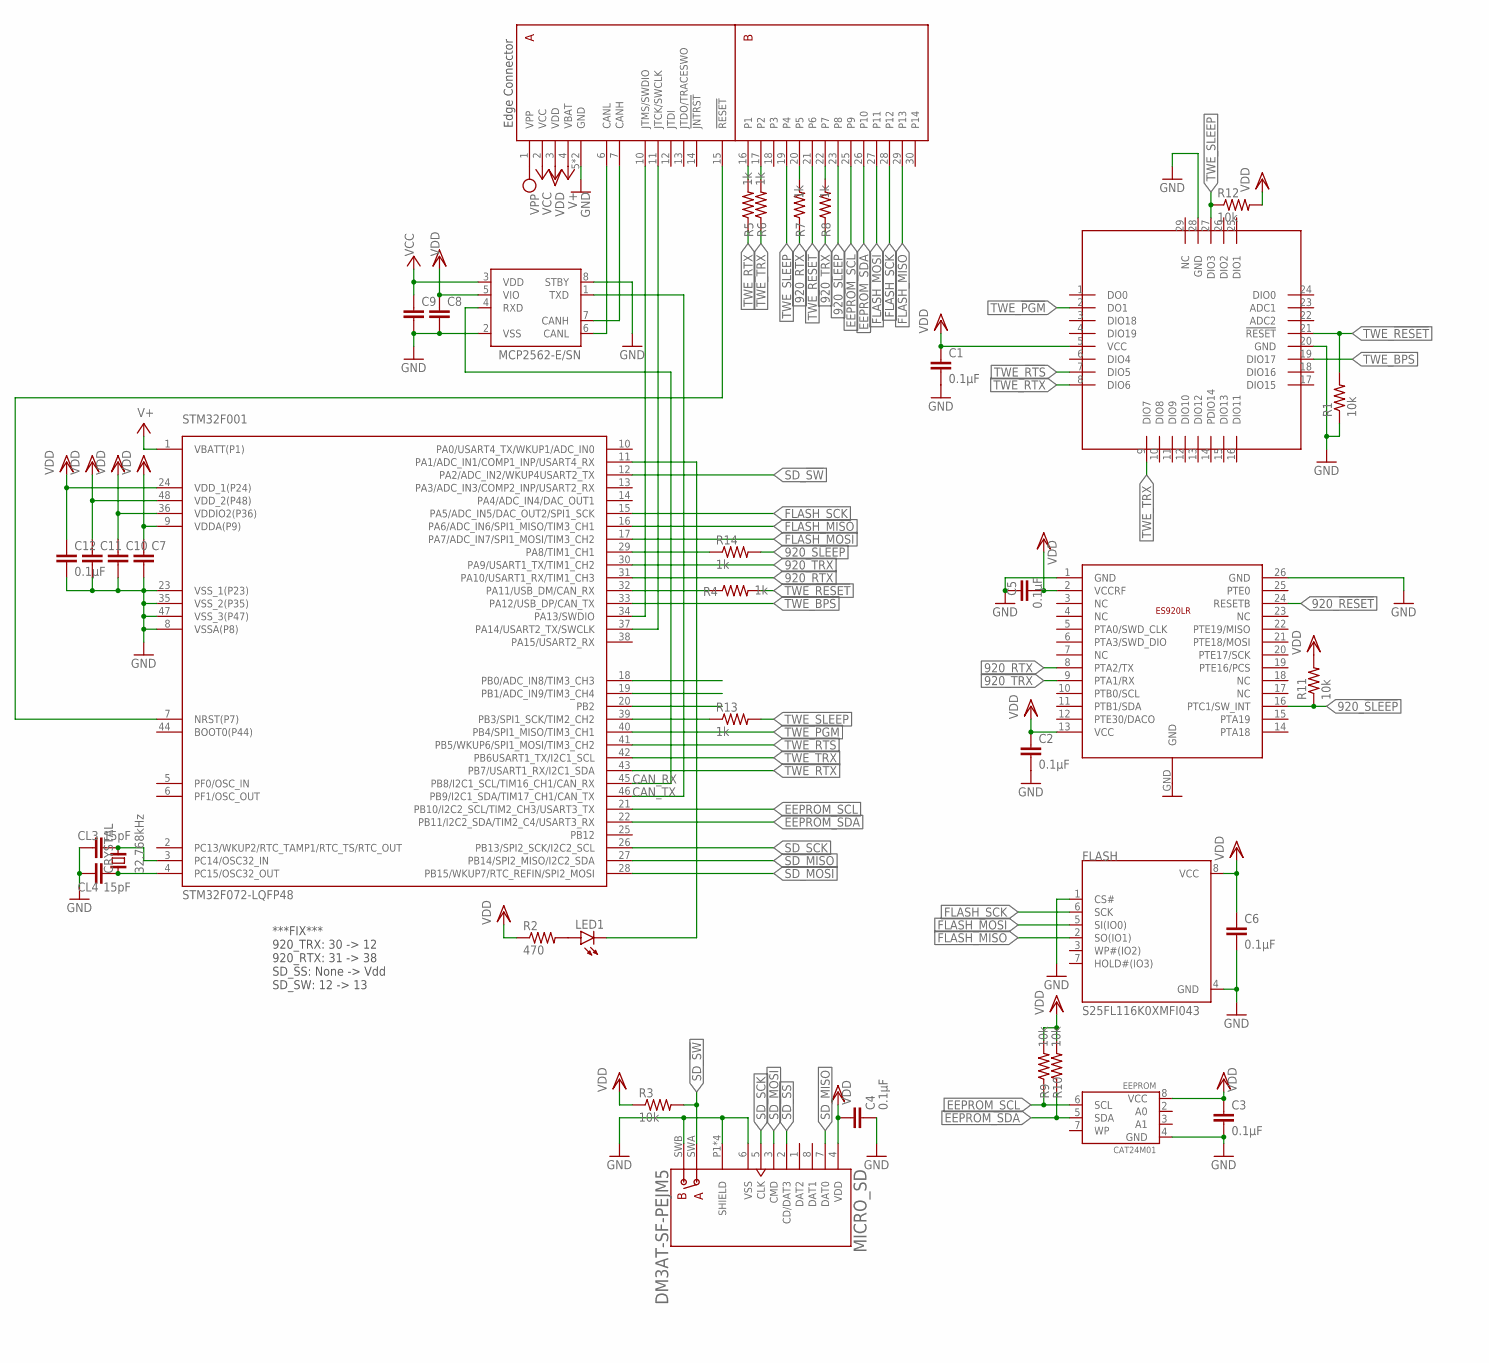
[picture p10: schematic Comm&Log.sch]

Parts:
C1, C2, C3, C4, C5, C6, C12: 0.1µF; C0603K
C7, C8, C9, C10, C11: C-EUC0603K; C0603K
CL3, CL4: 15pF; C0603K
CRYSTAL: 32.768kHz; FC-255
EEPROM: CAT24M01; SO-8
ES920LR: ES920LR
FLASH: S25FL116K0XMFI043; SOIC127P600X175-8N
LED1: LEDCHIP-LED0603; CHIP-LED0603
MCP1: MCP2562-E/SN; SOIC127P600X175-8N
MICRO_SD: DM3AT-SF-PEJM5; HRS_DM3AT-SF-PEJM5
R1, R3, R9, R10, R11, R12: 10k; R0603
R2: 470; R0603
R4, R5, R6, R7, R8, R13, R14: 1k; R0603
STM32F001: STM32F072-LQFP48; LQFP48
TWE-LITE: LITE
U$2: EDGE30

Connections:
920_!RESET!: ES920LR.24 (RESETB)
920_!SLEEP!: ES920LR.16 (PTC1/SW_INT), R11.1, R14.2, U$2.23 (P8)
920_!SLEEP!': R14.1, STM32F001.29 (PA8/TIM1_CH1)
920_RTX: ES920LR.8 (PTA2/TX), R7.1, STM32F001.31 (PA10/USART1_RX/TIM1_CH3)
920_RTX_: R7.2, U$2.20 (P5)
920_TRX: ES920LR.9 (PTA1/RX), R8.1, STM32F001.30 (PA9/USART1_TX/TIM1_CH2)
920_TRX_: R8.2, U$2.22 (P7)
CANH1: MCP1.7 (CANH), U$2.7 (CANH)
CANL1: MCP1.6 (CANL), U$2.6 (CANL)
CAN_RX: MCP1.4 (RXD), STM32F001.45 (PB8/I2C1_SCL/TIM16_CH1/CAN_RX)
CAN_TX: MCP1.1 (TXD), STM32F001.46 (PB9/I2C1_SDA/TIM17_CH1/CAN_TX)
EEPROM_SCL: EEPROM.6 (SCL), R9.1, STM32F001.21 (PB10/I2C2_SCL/TIM2_CH3/USART3_TX), U$2.25 (P9)
EEPROM_SDA: EEPROM.5 (SDA), R10.1, STM32F001.22 (PB11/I2C2_SDA/TIM2_C4/USART3_RX), U$2.26 (P10)
FLASH_MISO: FLASH.2 (SO(IO1)), STM32F001.16 (PA6/ADC_IN6/SPI1_MISO/TIM3_CH1), U$2.29 (P13)
FLASH_MOSI: FLASH.5 (SI(IO0)), STM32F001.17 (PA7/ADC_IN7/SPI1_MOSI/TIM3_CH2), U$2.27 (P11)
FLASH_SCK: FLASH.6 (SCK), STM32F001.15 (PA5/ADC_IN5/DAC_OUT2/SPI1_SCK), U$2.28 (P12)
GND: C1.2, C2.2, C3.2, C4.2, C5.1, C6.2, C7.2, C8.2, C9.2, C10.2, C11.2, C12.2, CL3.1, CL4.1, EEPROM.4 (GND), ES920LR.1 (GND), ES920LR.26 (GND), ES920LR.GND, FLASH.1 (CS#), FLASH.4 (GND), MCP1.2 (VSS), MCP1.8 (STBY), MICRO_SD.6 (VSS), MICRO_SD.P1 (SHIELD), MICRO_SD.P2 (SHIELD), MICRO_SD.P3 (SHIELD), MICRO_SD.P4 (SHIELD), MICRO_SD.SWB (B), R1.1, STM32F001.8 (VSSA(P8)), STM32F001.23 (VSS_1(P23)), STM32F001.35 (VSS_2(P35)), STM32F001.47 (VSS_3(P47)), TWE-LITE.20 (GND), TWE-LITE.28 (GND), U$2.5 (GND), U$2.8 (GND)
unnamed: R4.1, STM32F001.32 (PA11/USB_DM/CAN_RX)
unnamed: R6.2, U$2.17 (P2)
unnamed: R13.1, STM32F001.39 (PB3/SPI1_SCK/TIM2_CH2)
unnamed: CL4.2, CRYSTAL.1, STM32F001.4 (PC15/OSC32_OUT)
unnamed: CL3.2, CRYSTAL.2, STM32F001.3 (PC14/OSC32_IN)
unnamed: LED1.C, STM32F001.11 (PA1/ADC_IN1/COMP1_INP/USART4_RX)
unnamed: R5.2, U$2.16 (P1)
unnamed: LED1.A, R2.2
NRST1: STM32F001.7 (NRST(P7)), U$2.15 (!RESET!)
SD_!SS!: MICRO_SD.2 (CD/DAT3)
SD_!SW!: MICRO_SD.SWA (A), R3.2, STM32F001.12 (PA2/ADC_IN2/WKUP4USART2_TX)
SD_MISO: MICRO_SD.7 (DAT0), STM32F001.27 (PB14/SPI2_MISO/I2C2_SDA)
SD_MOSI: MICRO_SD.3 (CMD), STM32F001.28 (PB15/WKUP7/RTC_REFIN/SPI2_MOSI)
SD_SCK: MICRO_SD.5 (CLK), STM32F001.26 (PB13/SPI2_SCK/I2C2_SCL)
SWCLK1: STM32F001.37 (PA14/USART2_TX/SWCLK), U$2.11 (JTCK/SWCLK)
SWDIO1: STM32F001.34 (PA13/SWDIO), U$2.10 (JTMS/SWDIO)
TWE_!PGM!: STM32F001.40 (PB4/SPI1_MISO/TIM3_CH1), TWE-LITE.2 (DO1)
TWE_!RESET!: R1.2, R4.2, TWE-LITE.21 (!RESET!), U$2.21 (P6)
TWE_!RTS!: STM32F001.41 (PB5/WKUP6/SPI1_MOSI/TIM3_CH2), TWE-LITE.7 (DIO5)
TWE_BPS: STM32F001.33 (PA12/USB_DP/CAN_TX), TWE-LITE.19 (DIO17)
TWE_RTX: R5.1, STM32F001.43 (PB7/USART1_RX/I2C1_SDA), TWE-LITE.8 (DIO6)
TWE_SLEEP: R12.1, R13.2, TWE-LITE.27 (DIO3), U$2.19 (P4)
TWE_TRX: R6.1, STM32F001.42 (PB6USART1_TX/I2C1_SCL), TWE-LITE.9 (DIO7)
VBAT: STM32F001.1 (VBATT(P1)), U$2.4 (VBAT)
VCC: C9.1, MCP1.3 (VDD), U$2.2 (VCC)
VDD: C1.1, C2.1, C3.1, C4.1, C5.2, C6.1, C7.1, C8.1, C10.1, C11.1, C12.1, EEPROM.8 (VCC), ES920LR.2 (VCCRF), ES920LR.13 (VCC), FLASH.8 (VCC), MCP1.5 (VIO), MICRO_SD.4 (VDD), R2.1, R3.1, R9.2, R10.2, R11.2, R12.2, STM32F001.9 (VDDA(P9)), STM32F001.24 (VDD_1(P24)), STM32F001.36 (VDDIO2(P36)), STM32F001.48 (VDD_2(P48)), TWE-LITE.5 (VCC), U$2.3 (VDD)
VPP: U$2.1 (VPP)

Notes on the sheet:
***FIX*** 920_TRX: 30 -> 12 920_RTX: 31 -> 38 SD_SS: None -> Vdd SD_SW: 12 -> 13

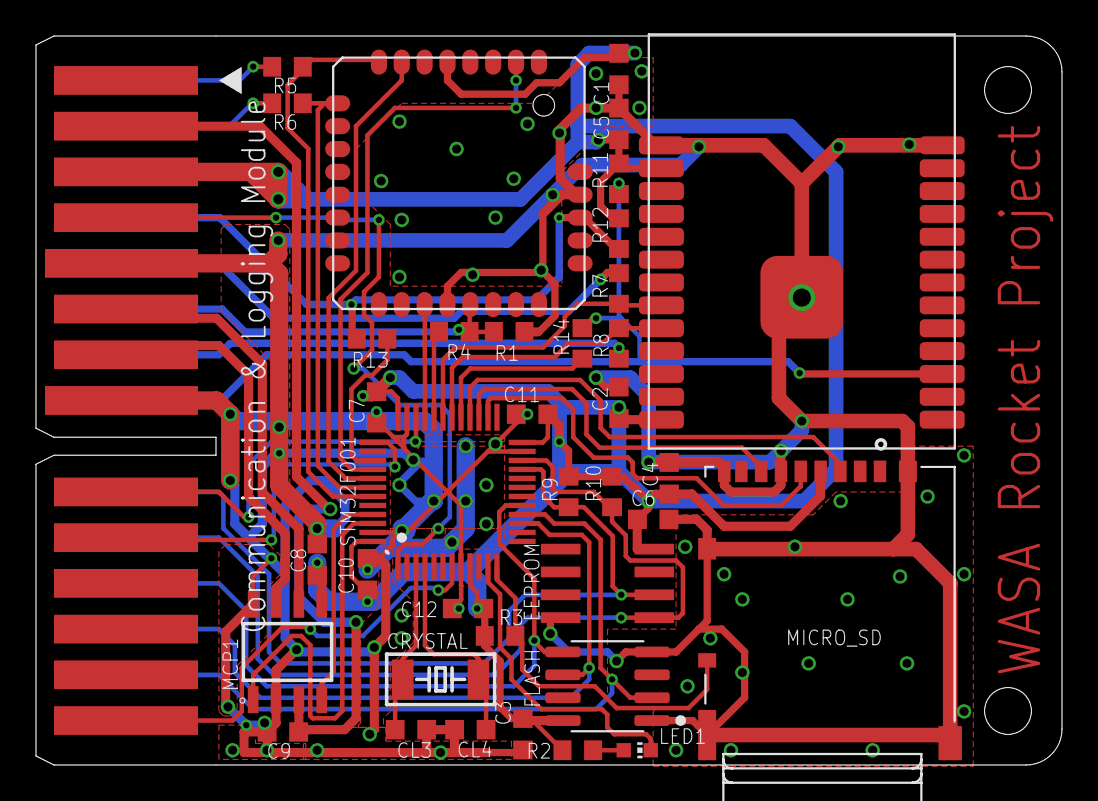
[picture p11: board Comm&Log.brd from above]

Board: 2 copper layers, 57.0 x 40.5 mm, 38 parts (0 on the bottom side), 41 nets.

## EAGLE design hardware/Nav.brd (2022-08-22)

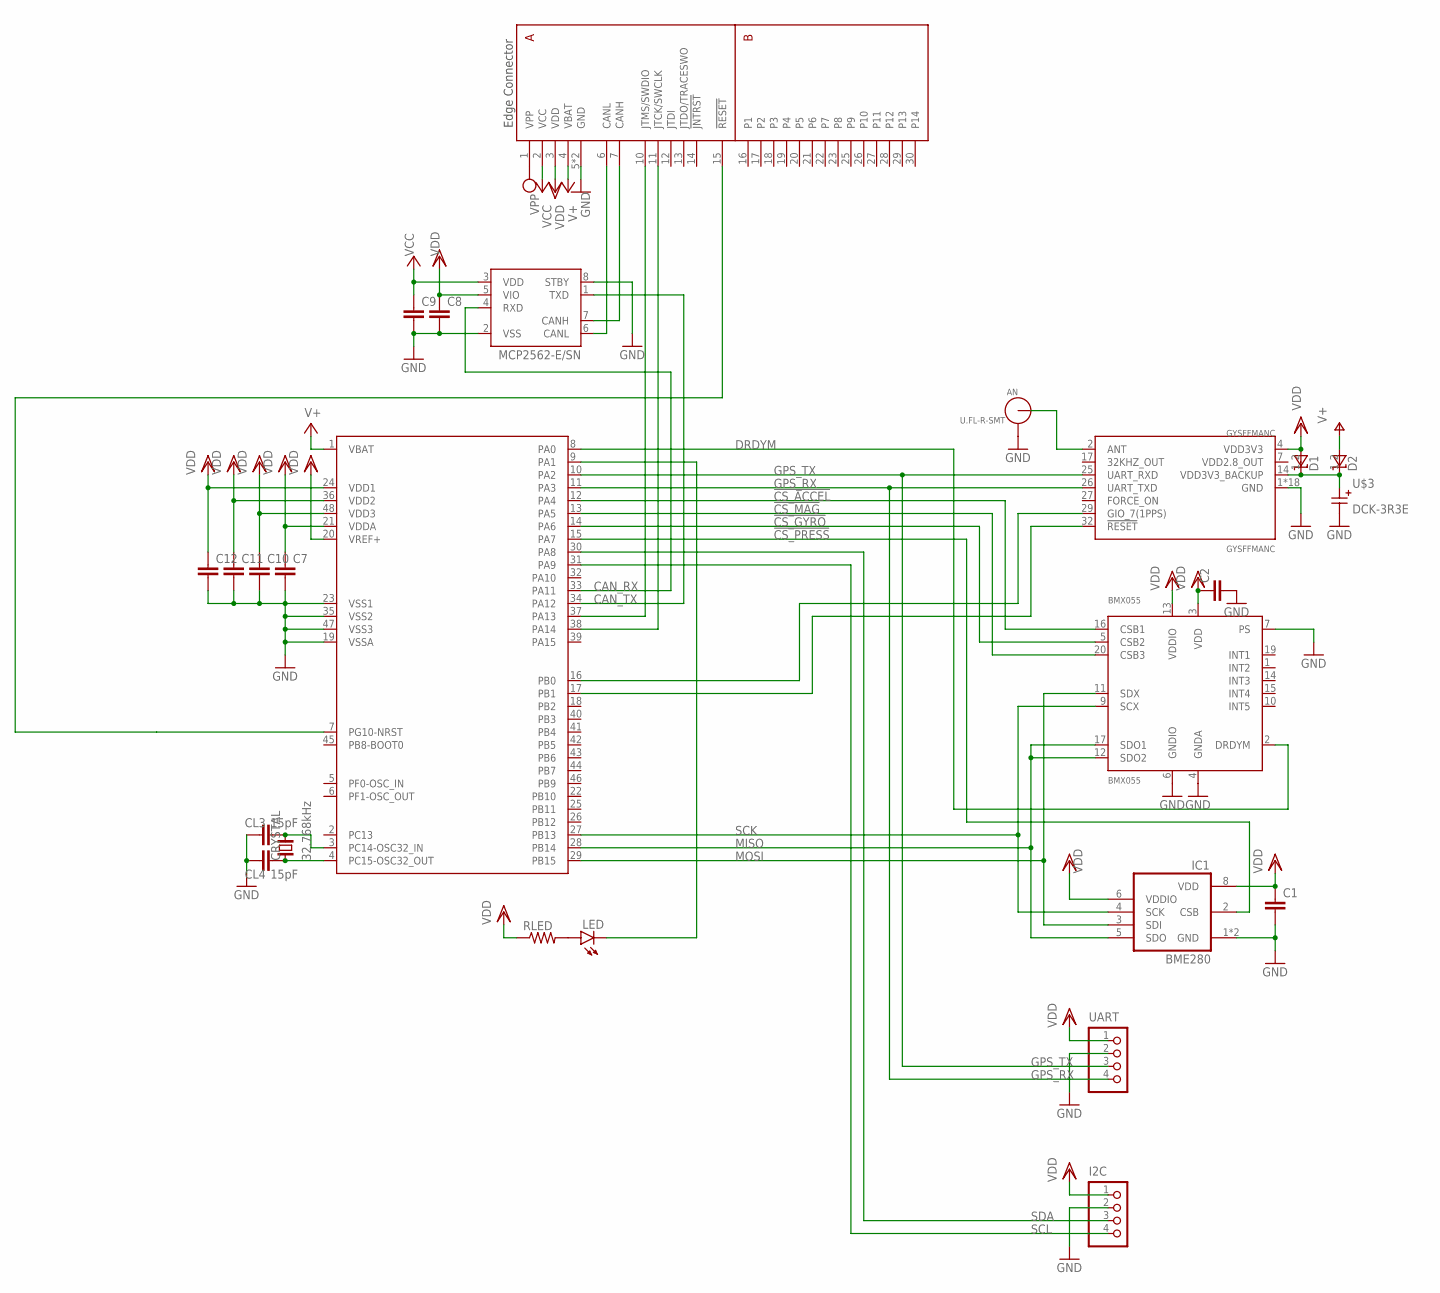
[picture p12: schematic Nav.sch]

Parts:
AN: U.FL-R-SMT; U.FL_SMT
BMX055: BMX055
C1, C2, C7, C8, C9, C10, C11, C12: C-EUC0603K; C0603K
CL3, CL4: 15pF; C0603K
CRYSTAL: 32.768kHz; FC-255
D1, D2: RB521S-30TE61; SODFL1608X70N
GYSFFMANC: GYSFFMANC
I2C: S4B-PH-K-S
IC1: BME280
LED: LEDCHIP-LED0603; CHIP-LED0603
MCP2562: MCP2562-E/SN; SOIC127P600X175-8N
RLED: R-US_R0603; R0603
U$1: STM32G431-LQFP48; LQFP48
U$2: EDGE30
U$3: DCK-3R3E; DC,DCK
UART: S4B-PH-K-S

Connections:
!CS_ACCEL!: BMX055.16 (CSB1), U$1.12 (PA4)
!CS_GYRO!: BMX055.5 (CSB2), U$1.14 (PA6)
!CS_MAG!: BMX055.20 (CSB3), U$1.13 (PA5)
!CS_PRESS!: IC1.2 (CSB), U$1.15 (PA7)
CANH1: MCP2562.7 (CANH), U$2.7 (CANH)
CANL1: MCP2562.6 (CANL), U$2.6 (CANL)
CAN_RX: MCP2562.4 (RXD), U$1.33 (PA11)
CAN_TX: MCP2562.1 (TXD), U$1.34 (PA12)
DRDYM: BMX055.2 (DRDYM), U$1.8 (PA0)
GND: AN.GND1, AN.GND2, BMX055.4 (GNDA), BMX055.6 (GNDIO), BMX055.7 (PS), C1.2, C2.2, C7.2, C8.2, C9.2, C10.2, C11.2, C12.2, CL3.1, CL4.1, GYSFFMANC.1 (GND), GYSFFMANC.3 (GND), GYSFFMANC.8 (GND), GYSFFMANC.10 (GND), GYSFFMANC.12 (GND), GYSFFMANC.22 (GND), GYSFFMANC.33 (GND), GYSFFMANC.36 (GND), GYSFFMANC.37 (GND), GYSFFMANC.38 (GND), GYSFFMANC.39 (GND), GYSFFMANC.40 (GND), GYSFFMANC.41 (GND), GYSFFMANC.42 (GND), GYSFFMANC.43 (GND), GYSFFMANC.44 (GND), GYSFFMANC.45 (GND), GYSFFMANC.46 (GND), I2C.2, IC1.1 (GND), IC1.7 (GND), MCP2562.2 (VSS), MCP2562.8 (STBY), U$1.19 (VSSA), U$1.23 (VSS1), U$1.35 (VSS2), U$1.47 (VSS3), U$2.5 (GND), U$2.8 (GND), U$3.-, UART.2
GPS_RX: GYSFFMANC.26 (UART_TXD), U$1.11 (PA3), UART.4
GPS_TX: GYSFFMANC.25 (UART_RXD), U$1.10 (PA2), UART.3
MISO: BMX055.12 (SDO2), BMX055.17 (SDO1), IC1.5 (SDO), U$1.28 (PB14)
MOSI: BMX055.11 (SDX), IC1.3 (SDI), U$1.29 (PB15)
unnamed: AN.SIG (ANT), GYSFFMANC.2 (ANT)
unnamed: GYSFFMANC.29 (GIO_7(1PPS)), U$1.16 (PB0)
unnamed: GYSFFMANC.32 (!RESET!), U$1.17 (PB1)
unnamed: U$1.7 (PG10-NRST), U$2.15 (!RESET!)
unnamed: LED.C, U$1.9 (PA1)
unnamed: CL4.2, CRYSTAL.1, U$1.4 (PC15-OSC32_OUT)
unnamed: CL3.2, CRYSTAL.2, U$1.3 (PC14-OSC32_IN)
unnamed: LED.A, RLED.2
SCK: BMX055.9 (SCX), IC1.4 (SCK), U$1.27 (PB13)
SCL: I2C.4, U$1.31 (PA9)
SDA: I2C.3, U$1.30 (PA8)
SWCLK1: U$1.38 (PA14), U$2.11 (JTCK/SWCLK)
SWDIO1: U$1.37 (PA13), U$2.10 (JTMS/SWDIO)
VBACKUP: D1.1 (K), D2.1 (K), GYSFFMANC.14 (VDD3V3_BACKUP), U$3.+
VBAT: D2.2 (A), U$1.1 (VBAT), U$2.4 (VBAT)
VCC: C9.1, MCP2562.3 (VDD), U$2.2 (VCC)
VDD: BMX055.3 (VDD), BMX055.13 (VDDIO), C1.1, C2.1, C7.1, C8.1, C10.1, C11.1, C12.1, D1.2 (A), GYSFFMANC.4 (VDD3V3), I2C.1, IC1.6 (VDDIO), IC1.8 (VDD), MCP2562.5 (VIO), RLED.1, U$1.20 (VREF+), U$1.21 (VDDA), U$1.24 (VDD1), U$1.36 (VDD2), U$1.48 (VDD3), U$2.3 (VDD), UART.1
VDD2.8_OUT: GYSFFMANC.7 (VDD2.8_OUT)
VPP: U$2.1 (VPP)


Board: 2 copper layers, 57.0 x 40.5 mm, 25 parts (0 on the bottom side), 31 nets.

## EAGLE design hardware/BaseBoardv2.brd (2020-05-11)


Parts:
A: CR22A-30D-2.54DS
B: CR22A-30D-2.54DS
C: CR22A-30D-2.54DS
CN1, CN2: B4B-PH-K-S
D: CR22A-30D-2.54DS
E: CR22A-30D-2.54DS
F: CR22A-30D-2.54DS
U$7: P2_7_1.27
U$8: PCI-E16X_DATA_EDGE; PCI-E_164_DATA_EDGE

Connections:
!JNTRST!: F.P14
!NRST!: F.P15, U$7.P12
A01: A.P16, U$8.A16
A02: A.P17, U$8.A17
A03: A.P18, U$8.A18
A04: A.P19, U$8.A19
A05: A.P20, U$8.A20
A06: A.P21, U$8.A21
A07: A.P22, U$8.A22
A08: A.P23, U$8.B16
A09: A.P24, U$8.B17
A10: A.P25, U$8.B18
A11: A.P26, U$8.B19
A12: A.P27, U$8.B20
A13: A.P28, U$8.B21
A14: A.P29, U$8.B22
A15: A.P30, U$8.B23
B01: B.P16, U$8.A26
B02: B.P17, U$8.A27
B03: B.P18, U$8.A28
B04: B.P19, U$8.A29
B05: B.P20, U$8.A30
B06: B.P21, U$8.A31
B07: B.P22, U$8.A32
B08: B.P23, U$8.B26
B09: B.P24, U$8.B27
B10: B.P25, U$8.B28
B11: B.P26, U$8.B29
B12: B.P27, U$8.B30
B13: B.P28, U$8.B31
B14: B.P29, U$8.B32
B15: B.P30, U$8.B33
C01: C.P16, U$8.A36
C02: C.P17, U$8.A37
C03: C.P18, U$8.A38
C04: C.P19, U$8.A39
C05: C.P20, U$8.A40
C06: C.P21, U$8.A41
C07: C.P22, U$8.A42
C08: C.P23, U$8.B36
C09: C.P24, U$8.B37
C10: C.P25, U$8.B38
C11: C.P26, U$8.B39
C12: C.P27, U$8.B40
C13: C.P28, U$8.B41
C14: C.P29, U$8.B42
C15: C.P30, U$8.B43
CANH: A.P7, B.P7, C.P7, CN1.3, CN2.3, D.P7, E.P7, F.P7
CANL: A.P6, B.P6, C.P6, CN1.2, CN2.2, D.P6, E.P6, F.P6
D01: D.P16, U$8.A46
D02: D.P17, U$8.A47
D03: D.P18, U$8.A48
D04: D.P19, U$8.A49
D05: D.P20, U$8.A50
D06: D.P21, U$8.A51
D07: D.P22, U$8.A52
D08: D.P23, U$8.B46
D09: D.P24, U$8.B47
D10: D.P25, U$8.B48
D11: D.P26, U$8.B49
D12: D.P27, U$8.B50
D13: D.P28, U$8.B51
D14: D.P29, U$8.B52
D15: D.P30, U$8.B53
E01: E.P16, U$8.A56
E02: E.P17, U$8.A57
E03: E.P18, U$8.A58
E04: E.P19, U$8.A59
E05: E.P20, U$8.A60
E06: E.P21, U$8.A61
E07: E.P22, U$8.A62
E08: E.P23, U$8.B56
E09: E.P24, U$8.B57
E10: E.P25, U$8.B58
E11: E.P26, U$8.B59
E12: E.P27, U$8.B60
E13: E.P28, U$8.B61
E14: E.P29, U$8.B62
E15: E.P30, U$8.B63
F01: F.P16, U$8.A66
F02: F.P17, U$8.A67
F03: F.P18, U$8.A68
F04: F.P19, U$8.A69
F05: F.P20, U$8.A70
F06: F.P21, U$8.A71
F07: F.P22, U$8.A72
F08: F.P23, U$8.B66
F09: F.P24, U$8.B67
F10: F.P25, U$8.B68
F11: F.P26, U$8.B69
F12: F.P27, U$8.B70
F13: F.P28, U$8.B71
F14: F.P29, U$8.B72
F15: F.P30, U$8.B73
GND: A.P5, A.P8, B.P5, B.P8, C.P5, C.P8, CN1.4, CN2.4, D.P5, D.P8, E.P5, E.P8, F.P5, F.P8, U$7.P5, U$7.P7, U$7.P11, U$8.A12, U$8.A13, U$8.A14, U$8.A15, U$8.A23, U$8.A24, U$8.A25, U$8.A33, U$8.A34, U$8.A35, U$8.A43, U$8.A44, U$8.A45, U$8.A53, U$8.A54, U$8.A55, U$8.A63, U$8.A64, U$8.A65, U$8.B12, U$8.B13, U$8.B14, U$8.B15, U$8.B24, U$8.B25, U$8.B34, U$8.B35, U$8.B44, U$8.B45, U$8.B54, U$8.B55, U$8.B64, U$8.B65
JCLK: U$7.P9
JCLK/SWCLK: F.P11, U$7.P6
JTDI: F.P12, U$7.P10
JTDO/SWO: F.P13, U$7.P8
JTMS/SWDIO: F.P10, U$7.P4
T_VCC: U$7.P3
VBU: A.P4, B.P4, C.P4, D.P4, E.P4, F.P4
VCC: A.P2, B.P2, C.P2, D.P2, E.P2, F.P2
VCP_RX: U$7.P13
VCP_TX: U$7.P14
VDD: A.P3, B.P3, C.P3, D.P3, E.P3, F.P3
VPP: A.P1, B.P1, C.P1, CN1.1, CN2.1, D.P1, E.P1, F.P1


Board: 2 copper layers, 71.1 x 55.2 mm, 10 parts (0 on the bottom side), 102 nets.

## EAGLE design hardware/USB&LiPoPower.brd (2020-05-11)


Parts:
BACKUP: SK-12D01-VG4
C3: 2.2µF; C0603K
C4: 0.33µF; C0603K
C5, C6, C7, C8, C9, C10, C11, C12, C13: 0.1µF; C0603K
C14, C15: 1nF; C0603K
C16, C17: 47µF; UD-5X5,8_NICHICON
CHARGER: MCP73831; SOT23-5L
CR1201: CH291-1220LF
D1, D2, D3, D4, D5: RB160M-30TR; SODFL3516X90N
I: 100µH; NR10050
IC1, IC2: 4066D; SO14
IC3: HT7750A_SOT23-3; SOT95P190X145-3N
IC4: I-02247_NJM2845; TO252
LED: LEDCHIP-LED0603; CHIP-LED0603
LIPO: S2B-PH-K-S
MCP2562: MCP2562-E/SN; SOIC127P600X175-8N
MICRO_USB: MICRO-USB
OP: NJM2904M; SO-8
POWER: SK-12D01-VG4
R1, R2, R5, R6, R7, R8, R10, R17: 10k; R0603
R3: 100k; R0603
R4, R9, R11, R12, R13, R14, R15, R16, R18: 1k; R0603
RC1, RC2: 1k; R0603
RF1, RF2: 33k; R0603
RLED: 1K; R0603
RPROG: 4.7k; R0603
RS1, RS2: 1k; R0603
STM32F001: STM32F072-LQFP48; LQFP48
T1, T2, T3, T4: IRLML5203; MICRO3
U$2: EDGE30
VCCC: ACS711ELCTR-12AB-T; SOIC8
VDDC: ACS711ELCTR-12AB-T; SOIC8

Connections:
3.3V: C3.1, IC4.3 (VOUT), R7.2, VDDC.1 (IP+1), VDDC.2 (IP+2)
3.3VC: IC1.3 (B), R15.1, STM32F001.15 (PA5/ADC_IN5/DAC_OUT2/SPI1_SCK)
3.3VC': IC1.4 (A), OP.7 (OUT), RF2.2
3.3VC_OUT: C15.1, OP.5 (IN+), RC2.2
3.3VC_OUT': RC2.1, VDDC.7 (VOUT)
5V: D5.1 (K), R5.2, T3.2 (S), VCCC.1 (IP+1), VCCC.2 (IP+2)
5VC: IC1.2 (B), R16.1, STM32F001.14 (PA4/ADC_IN4/DAC_OUT1)
5VC': IC1.1 (A), OP.1 (OUT), RF1.2
5VC_OUT: C14.1, OP.3 (IN+), RC1.2
5VC_OUT': RC1.1, VCCC.7 (VOUT)
!HIL!: IC1.5 (C), IC1.13 (C), IC2.5 (C), IC2.6 (C), IC2.12 (C), IC2.13 (C), R9.1, R10.1
BAT+: BACKUP.B, CR1201.+
CANH1: MCP2562.7 (CANH), U$2.7 (CANH)
CANL1: MCP2562.6 (CANL), U$2.6 (CANL)
CAN_RX: MCP2562.4 (RXD), STM32F001.45 (PB8/I2C1_SCL/TIM16_CH1/CAN_RX)
CAN_TX: MCP2562.1 (TXD), STM32F001.46 (PB9/I2C1_SDA/TIM17_CH1/CAN_TX)
GND: C3.2, C4.2, C5.2, C6.2, C7.2, C8.2, C9.2, C10.2, C11.2, C12.2, C13.2, C14.2, C15.2, C16.-, C17.-, CHARGER.2 (VSS), CR1201.-, IC1.7 (VSS), IC2.7 (VSS), IC3.1 (GND), IC4.2 (GND), LIPO.2, MCP2562.2 (VSS), MCP2562.8 (STBY), MICRO_USB.5 (GND), MICRO_USB.GND1 (GND), MICRO_USB.GND2 (GND), OP.4 (V-), POWER.A, R1.1, R4.1, R6.1, R8.1, RPROG.1, RS1.1, RS2.1, STM32F001.8 (VSSA(P8)), STM32F001.23 (VSS_1(P23)), STM32F001.35 (VSS_2(P35)), STM32F001.47 (VSS_3(P47)), U$2.5 (GND), U$2.8 (GND), VCCC.5 (GND), VDDC.5 (GND)
LIPO+: CHARGER.3 (VBAT), D3.2 (A), LIPO.1, T2.2 (S)
unnamed: CHARGER.5 (PROG), RPROG.2
unnamed: CHARGER.1 (STAT), R17.2
unnamed: LED.C, RLED.1
unnamed: OP.2 (IN-), RF1.1, RS1.2
unnamed: OP.6 (IN-), RF2.1, RS2.2
unnamed: POWER.C, R3.1, T1.1 (G), T2.1 (G)
unnamed: D3.1 (K), D4.1 (K), R3.2
unnamed: R16.2, U$2.30 (P14)
unnamed: R15.2, U$2.29 (P13)
unnamed: R14.2, U$2.28 (P12)
unnamed: R13.2, U$2.27 (P11)
unnamed: R12.2, U$2.26 (P10)
unnamed: R11.2, U$2.25 (P9)
unnamed: RLED.2, STM32F001.2 (PC13/WKUP2/RTC_TAMP1/RTC_TS/RTC_OUT)
unnamed: R9.2, U$2.16 (P1)
unnamed: R18.2, U$2.17 (P2)
NRST1: STM32F001.7 (NRST(P7)), U$2.15 (!RESET!)
PVCC: IC2.8 (A), R5.1, R6.2
PVDD: IC2.11 (A), R7.1, R8.2
PVPP: IC2.4 (A), R2.1, R4.2
STAT: R17.1, R18.1, STM32F001.11 (PA1/ADC_IN1/COMP1_INP/USART4_RX)
SVBU: IC2.2 (B), R14.1, STM32F001.16 (PA6/ADC_IN6/SPI1_MISO/TIM3_CH1)
SVCC: IC2.9 (B), R11.1, STM32F001.19 (PB1/ADC_IN9/TIM3_CH4)
SVDD: IC2.10 (B), R12.1, STM32F001.18 (PB0/ADC_IN8/TIM3_CH3)
SVPP: IC2.3 (B), R13.1, STM32F001.17 (PA7/ADC_IN7/SPI1_MOSI/TIM3_CH2)
SWCLK1: STM32F001.37 (PA14/USART2_TX/SWCLK), U$2.11 (JTCK/SWCLK)
SWDIO1: STM32F001.34 (PA13/SWDIO), U$2.10 (JTMS/SWDIO)
USB_5V: D4.2 (A), MICRO_USB.1 (VCC), T1.2 (S)
USB_D+: MICRO_USB.3 (D+), STM32F001.33 (PA12/USB_DP/CAN_TX)
USB_D-: MICRO_USB.2 (D-), STM32F001.32 (PA11/USB_DM/CAN_RX)
VBU: BACKUP.C, IC2.1 (A), STM32F001.1 (VBATT(P1)), U$2.4 (VBAT)
VCC: C9.1, LED.A, MCP2562.3 (VDD), U$2.2 (VCC), VCCC.3 (IP-1), VCCC.4 (IP-2)
VCCG_IN: D1.2 (A), I.2, IC3.2 (LX)
VCC_GEN: C17.+, D1.1 (K), IC3.3 (VOUT), T3.3 (D)
VCC_USB: CHARGER.4 (VDD), D2.2 (A), D5.2 (A), R1.2, T1.3 (D), T3.1 (G), T4.1 (G)
VDD: C5.1, C6.1, C7.1, C8.1, C10.1, C11.1, C12.1, C13.1, IC1.14 (VDD), IC2.14 (VDD), MCP2562.5 (VIO), OP.8 (V+), R10.2, STM32F001.9 (VDDA(P9)), STM32F001.24 (VDD_1(P24)), STM32F001.36 (VDDIO2(P36)), STM32F001.48 (VDD_2(P48)), U$2.3 (VDD), VCCC.8 (VCC), VDDC.3 (IP-1), VDDC.4 (IP-2), VDDC.8 (VCC)
VLIPO: C16.+, I.1, T2.3 (D), T4.3 (D)
VPP: C4.1, D2.1 (K), IC4.1 (VIN), R2.2, T4.2 (S), U$2.1 (VPP)

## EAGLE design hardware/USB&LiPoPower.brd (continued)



Board: 2 copper layers, 57.0 x 40.5 mm, 68 parts (14 on the bottom side), 56 nets.

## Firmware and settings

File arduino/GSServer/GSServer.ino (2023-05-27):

#define CONFIG_ASYNC_TCP_USE_WDT 0

#include <TinyGPS++.h>
#include <WiFi.h>
#include <ESPmDNS.h>
#include <ESPAsyncWebServer.h>
#include <AsyncJson.h>
#include <SPIFFS.h>
#include <CAN.h>
#include "command.hpp"
#include "LCD.h"

#define AP_MODE

#define GPS_RX_PIN 5
#define GPS_TX_PIN 18
#define CAN_RX_PIN 32
#define CAN_TX_PIN 33
#define LED_PIN 2
#define SWITCH_PIN_1 12
#define SWITCH_PIN_2 13
#define SWITCH_PIN_3 14

#define CAN_BAUD 125000
static const uint32_t GPSBaud = 9600;

#define RETURN_COMMAND_MAX 100
#define SEND_COMMAND_FREQ 1
#define BLINK_MS 50

#define GPS_SWITCH_FREQ 0.1

const char ssid[] = "Rockoon-GS1";
const char pass[] = "rockoon-gs1";
/* const char ssid[] = "Rockoon-GS2"; */
/* const char pass[] = "rockoon-gs2"; */
const IPAddress ip(192,168,1,1);
const IPAddress subnet(255,255,255,0);
AsyncWebServer server(80);


LCD lcd;
TinyGPSPlus gps;
HardwareSerial ss(2);

CANChannel can_channel;
HexChannel hex_channel;

Command* received_remote_commands;
uint32_t received_remote_count;
uint32_t received_remote_max;

Command* received_local_commands;
uint32_t received_local_count;
uint32_t received_local_max;

enum class SwitchState {
  NotSelected,
  NoLaunch,
  AllowLaunch,
};

SwitchState switch_state = SwitchState::NotSelected;
unsigned long blink_ms;
unsigned long sent_command_ms;

float launcher_lat;
float launcher_lng;
uint32_t launcher_gps_received;


void setup() {
  Serial.begin(115200);
  ss.begin(GPSBaud, SERIAL_8N1, GPS_RX_PIN, GPS_TX_PIN);
  Wire.begin(21, 22);

  /* pinMode(21, INPUT_PULLUP); */
  /* pinMode(22, INPUT_PULLUP); */

  pinMode(LED_PIN, OUTPUT);
  pinMode(SWITCH_PIN_1, INPUT_PULLUP);
  pinMode(SWITCH_PIN_2, INPUT_PULLUP);
  pinMode(SWITCH_PIN_3, INPUT_PULLUP);

  digitalWrite(LED_PIN, HIGH);

  i2c_scanner();

  lcd.begin();

  init_datastore();

  delay(1000);

  init_server();

  delay(1000);

  CAN.setPins(CAN_RX_PIN, CAN_TX_PIN);
  CAN.begin(CAN_BAUD * 2);
  /* CAN.onReceive(onCANReceive); */

  digitalWrite(LED_PIN, LOW);

  char line1[] = "GPS Unavailable ";
  char line2[] = "----------------";

  strncpy(lcd.line1, line1, 16);
  strncpy(lcd.line2, line2, 16);
  lcd.show();
}

void loop() {

  int packetSize = CAN.parsePacket();
  if (packetSize > 0) onCANReceive(packetSize);

  // Read GPS
  while(ss.available()){
    char c = ss.read();
    gps.encode(c);
  }

  // Update location
  if (!gps.location.isValid()) {

  }
  else if (gps.location.isUpdated()) {
    /* struct tm t; */
    /* t.tm_year  = gps.date.year() - 1900; */
    /* t.tm_mon   = gps.date.month() - 1; */
    /* t.tm_mday  = gps.date.day(); */
    /* t.tm_hour  = gps.time.hour(); */
    /* t.tm_min   = gps.time.minute(); */
    /* t.tm_sec   = gps.time.second(); */
    /* t.tm_isdst = -1; */
    /* time_t epoch = mktime(&t); */

    Command position('P', 0, 0, 4);
    position.entries[0].set('O', (float)gps.location.lng());
    position.entries[1].set('A', (float)gps.location.lat());
    position.entries[2].set('H', (float)gps.altitude.meters());
    position.entries[3].set('D', (uint32_t)gps.date.value());
    position.entries[3].set('T', (uint32_t)gps.time.value());

    can_channel.tx.push(position);
    sendCAN();

    addReceivedCommand(position);
  }

  int step = int(millis() * GPS_SWITCH_FREQ) % 1000;
  if (step < 500 && step % 10 == 0) {
    strcpy(lcd.line1, "GS      ");
    if (gps.location.age() >= 100000) {
      snprintf(lcd.line2, 7, "N/A  ");
    }
    else {
      snprintf(lcd.line2, 7, "%3.1fs ", (gps.location.age() / 1000.0));
    }
    printDegree(lcd.line1 + 7, gps.location.lng());
    printDegree(lcd.line2 + 7, gps.location.lat());
    /* snprintf(lcd.line1 + 6, 11, "%3.7f", gps.location.lng()); */
    /* snprintf(lcd.line2 + 6, 11, "%3.7f", gps.location.lat()); */
    lcd.show();
  }
  else if (step >= 500 && step % 10 == 0) {
    strcpy(lcd.line1, "L       ");
    if (millis() - launcher_gps_received >= 100000) {
      snprintf(lcd.line2, 8, "N/A     ");
    }
    else {
      snprintf(lcd.line2, 8, "%3.1fs   ",
               (millis() - launcher_gps_received) / 1000.0);
    }
    printDegree(lcd.line1 + 7, launcher_lng);
    printDegree(lcd.line2 + 7, launcher_lat);
    /* snprintf(lcd.line1 + 6, 11, "%3.7f", launcher_lng); */
    /* snprintf(lcd.line2 + 6, 11, "%3.7f", launcher_lat); */
    lcd.show();
  }

  lcd.update();

  /* server.handleClient(); */

  /* Serial.print("data: "); */
  /* Serial.println(received_count); */

  /* delay(50); */

  /* addDummyCANData(); */

  if (millis() - blink_ms >= BLINK_MS) {
    digitalWrite(LED_PIN, LOW);
  }

  if      (!digitalRead(SWITCH_PIN_2)) switch_state = SwitchState::NotSelected;
  else if (!digitalRead(SWITCH_PIN_1)) switch_state = SwitchState::NoLaunch;
  else if (!digitalRead(SWITCH_PIN_3)) switch_state = SwitchState::AllowLaunch;
  else                                 switch_state = SwitchState::NotSelected;

  // Send mode command
  if (millis() > sent_command_ms + 1000 / SEND_COMMAND_FREQ) {
    printSwitchState();

    if (switch_state != SwitchState::NotSelected) {
      Command command('m', 'L', 0, 1);
      uint8_t type = switch_state == SwitchState::AllowLaunch ? 'A' : 'N';
      command.entries[0].set(type);

      can_channel.tx.push(command);
      sendCAN();
      addReceivedCommand(command);
    }
    sent_command_ms = millis();
  }
}

void printDegree(char* buf, float deg) {
  int d = (int)deg;
  int m = (int)((deg - d) * 60);
  int s = (int)(((deg - d) * 60 - m) * 60);
  sprintf(buf, "%3d'%02d'%02d", (int)d, (int)m, (int)s);
}


void onCANReceive(int packetSize) {
  if (CAN.packetRtr()) return;

  uint8_t id = CAN.packetId();
  uint8_t len = CAN.packetDlc();

  /* Serial.print("CAN R  "); */
  /* Serial.print(id); */
  /* Serial.print(" "); */
  /* Serial.print(len); */
  /* Serial.print(": "); */

  uint8_t data[8];

  for (int n = 0; n < len; n++) {
    data[n] = CAN.read();
    /* Serial.print(data[n], HEX); */
  }

  /* Serial.println(); */

  if (can_channel.receive(id, data, len)) {
    addReceivedCommand(can_channel.rx);

    if (can_channel.rx.id == 'n') {
      union Payload p;
      if (can_channel.rx.get('A', 0, p)) {
        launcher_lat = p.float_;
        launcher_gps_received = millis();
      }
      if (can_channel.rx.get('O', 0, p)) {
        launcher_lng = p.float_;
        launcher_gps_received = millis();
      }
    }
  }
}


void sendCAN() {
	while (true) {
		if (can_channel.isReceiving()) return;

		uint16_t std_id;
		uint8_t len;
    uint8_t data[8];

		uint8_t remains = can_channel.send(std_id, data, len);

		if (len == 0) return;

    CAN.beginPacket(std_id);
    for (int n = 0; n < len; n++) CAN.write(data[n]);
    CAN.endPacket();

		if (remains == 0) break;
	}
}

void addReceivedCommand(const Command& c) {
  Command command = c;
  command.entries[command.size].set('t', (uint32_t)(millis()));
  command.size += 1;

  if (command.from == 0) {
    received_local_commands[received_local_count % received_local_max] =
      command;
    received_local_count++;

    Serial.print("local: ");
    Serial.println(received_local_count);
  }
  else {
    received_remote_commands[received_remote_count % received_remote_max] =
      command;
    received_remote_count++;

    Serial.print("remote: ");
    Serial.println(received_remote_count);
  }

  blink();
}


void handleDataRequest(AsyncWebServerRequest *request, bool local = false) {
  uint32_t received_count =
    local ? received_local_count : received_remote_count;
  uint32_t received_max =
    local ? received_local_max : received_remote_max;

  AsyncWebParameter *p = request->getParam("index");
  int request_index;

  if (p == NULL) request_index = 0;
  else request_index = p->value().toInt();

  uint32_t index_from = request_index;
  if (request_index < 0) index_from = 0;
  else if (request_index > received_count)
    index_from = received_count;

  String response;

  int index = index_from;

  for (int n = 0; n < RETURN_COMMAND_MAX; n++) {
    if (index == received_count) break;

    hex_channel.tx.push
      ((local ? received_local_commands : received_remote_commands)
       [index % received_max]);

    uint8_t buf[14];
    uint8_t len;
    while (true) {
      int remains = hex_channel.send(buf, len);
      response += String((char*)buf);
      if (remains <= 0) break;
    }

    index++;
    if (index == received_max) index = 0;
  }

  log_d("requested %s data: %d, return %d to %d, %d chars",
        local ? "local" : "remote", request_index, index_from, index,
        response.length());

  request->send(200, "text/plain", String(index) + '\n' + response);
}



bool init_server() {
  if(!SPIFFS.begin(true)){
    Serial.println("An Error has occurred while mounting SPIFFS");
    return false;
  }

  WiFi.softAP(ssid, pass);
  delay(100);
  WiFi.softAPConfig(ip, ip, subnet);
  IPAddress myIP = WiFi.softAPIP();

  Serial.print("SSID: ");
  Serial.println(ssid);
  Serial.print("AP IP address: ");
  Serial.println(myIP);

  server.on("/remote", HTTP_GET, [](AsyncWebServerRequest *request) {
      handleDataRequest(request, false);
    });
  server.on("/local", HTTP_GET, [](AsyncWebServerRequest *request) {
      handleDataRequest(request, true);
    });
  server.serveStatic("/", SPIFFS, "/").setDefaultFile("index.html");
  server.onNotFound([](AsyncWebServerRequest *request) {
      request->send(404, "text/plain", "File Not Found");
    });


  DefaultHeaders::Instance().addHeader("Access-Control-Allow-Origin", "*");
  DefaultHeaders::Instance().addHeader("Access-Control-Allow-Headers", "*");

  /* server.enableCORS(); */

  server.begin();


  MDNS.begin("gs");
  MDNS.addService("http", "tcp", 80);

  Serial.println("Server started");

  return true;
}




bool init_datastore() {
  psramInit();
  log_d("Total heap: %d", ESP.getHeapSize());
  log_d("Free heap: %d", ESP.getFreeHeap());
  log_d("Total PSRAM: %d", ESP.getPsramSize());
  log_d("Free PSRAM: %d", ESP.getFreePsram());

  int tlm_mem_size = ESP.getFreePsram() / 3;
  int gs_mem_size = ESP.getFreePsram() / 3;

  received_remote_commands = (Command*)ps_malloc(tlm_mem_size);
  received_remote_max = tlm_mem_size / sizeof(Command);
  received_remote_count = 0;


  received_local_commands = (Command*)ps_malloc(gs_mem_size);
  received_local_max = gs_mem_size / sizeof(Command);
  received_local_count = 0;

  if (received_remote_commands == NULL || received_local_commands == NULL) {
    Serial.println("Failed to alloc memory");
    return false;
  }


  Serial.print("Allocated ");
  Serial.print(received_local_max);
  Serial.print(" + ");
  Serial.println(received_local_max);

  return true;
}



void addDummyCANData() {
  Command command('B', 0, 0, 5);
  command.entries[0].set('P', (float)(9.0 + random(-50, 50) / 100.0));
  command.entries[1].set('C', (float)(5.0 + random(-50, 50) / 100.0));
  command.entries[2].set('D', (float)(3.3 + random(-50, 50) / 100.0));
  command.entries[3].set('c', (float)(random(0, 100) / 100.0));
  command.entries[4].set('d', (float)(random(0, 100) / 100.0));

  addReceivedCommand(command);
}

void blink() {
  blink_ms = millis();
  digitalWrite(LED_PIN, HIGH);
}

void printSwitchState() {
  switch (switch_state) {
  case SwitchState::NotSelected:
    Serial.println("Switch: Not selected");
    break;
  case SwitchState::NoLaunch:
    Serial.println("Switch: Abort");
    break;
  case SwitchState::AllowLaunch:
    Serial.println("Switch: Launch");
    break;
    }
}

void i2c_scanner() {
    byte error, address;
    int nDevices;

    Serial.println("I2C Scanner");
    Serial.println("Scanning...");

    nDevices = 0;
    for(address = 1; address < 127; address++ )
        {
            // The i2c_scanner uses the return value of
            // the Write.endTransmisstion to see if
            // a device did acknowledge to the address.
            Wire.beginTransmission(address);
            error = Wire.endTransmission();

            if (error == 0)
                {
                    Serial.print("I2C device found at address 0x");
                    if (address<16)
                        Serial.print("0");
                    Serial.print(address,HEX);
                    Serial.println("  !");

                    nDevices++;
                }
            else if (error==4)
                {
                    Serial.print("Unknown error at address 0x");
                    if (address<16)
                        Serial.print("0");
                    Serial.println(address,HEX);
                }
            else {
                //      Serial.println(error);
            }
        }
    if (nDevices == 0)
        Serial.println("No I2C devices found\n");
    else
        Serial.println("done\n");
}

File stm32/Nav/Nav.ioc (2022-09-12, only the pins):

Mcu.UserName=STM32G431C6Tx
PA0.GPIO_Label=DRDYM
PA0.Signal=GPIO_Input
PA1.GPIO_Label=LED
PA1.Signal=GPIO_Output
PA11.GPIO_Label=CAN_RX
PA11.Signal=FDCAN1_RX
PA12.GPIO_Label=CAN_TX
PA12.Signal=FDCAN1_TX
PA13.Signal=SYS_JTMS-SWDIO
PA14.Signal=SYS_JTCK-SWCLK
PA2.GPIO_Label=GPS_TX
PA2.Signal=USART2_TX
PA3.GPIO_Label=GPS_RX
PA3.Signal=USART2_RX
PA4.GPIO_Label=CS_ACCL
PA4.Signal=GPIO_Output
PA5.GPIO_Label=CS_MAG
PA5.Signal=GPIO_Output
PA6.GPIO_Label=CS_GYRO
PA6.Signal=GPIO_Output
PA7.GPIO_Label=CS_PRES
PA7.Signal=GPIO_Output
PA8.GPIO_Label=I2C_SDA
PA8.Signal=I2C2_SDA
PA9.GPIO_Label=I2C_SCL
PA9.Signal=I2C2_SCL
PB13.GPIO_Label=SPI_SCK
PB13.Signal=SPI2_SCK
PB14.GPIO_Label=SPI_MISO
PB14.Signal=SPI2_MISO
PB15.GPIO_Label=SPI_MOSI
PB15.Signal=SPI2_MOSI

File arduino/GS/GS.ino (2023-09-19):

#include <EEPROM.h>
#include <WiFi.h>
#include <WiFiMulti.h>
#include <WiFiClientSecure.h>
#include <WebSocketsClient.h>
#include <WiFiUdp.h>
#include <NTPClient.h>
#include <esp_task_wdt.h>
#include <CAN.h>
#include <TinyGPS++.h>
#include <FastCRC.h>
#include <PacketSerial.h>

#include <CANBus.hpp>
#include <Buffer.hpp>
#include <Packet.hpp>
#include "LCD.h"

#define ROCKET 0x01
#define LAUNCHER 0x02
#define GS1 0x06
#define GS2 0x05

#define UNIT GS2

#define NODE 'G'

constexpr char source[] = "GS2";
constexpr char system_id[] = "launch2023";

// constexpr bool ssl = false;
// constexpr char server[] = "Yuukis-MacBook-Pro-M2.local";
// constexpr unsigned port = 8888;
constexpr bool ssl = true;
constexpr char server[] = "telemeter.fujiy.dev";
constexpr unsigned port = 443;

// #define BUS_DEBUG_SERIAL

#define GPS_RX_PIN 5
#define GPS_TX_PIN 18
#define LED_PIN 2
#define SWITCH_PIN_1 12
#define SWITCH_PIN_2 13
#define SWITCH_PIN_3 14

#define CAN_BAUD 1000000
#define GPS_BAUD 9600

#define SEND_COMMAND_FREQ 0.2
#define SEND_LOCATION_FREQ 0.2
#define BLINK_MS 50

#define GPS_SWITCH_FREQ 0.1


#define NUM_AP 8
#define SSID_LEN 16
#define PASSWORD_LEN 16

#define BUS_BUF_SIZE 65536


TaskHandle_t thp[1];

WiFiMulti wifiMulti;
WiFiUDP udp;
NTPClient ntp(udp, "ntp.nict.jp", 0, 60000);

WebSocketsClient webSocket;

bool wifi_connected = false;

unsigned long epoch_s;
unsigned long epoch_s_start_millis = 0;

CANBus bus(NODE);

struct UploadPacket {
  uint32_t ms;
  uint8_t buf[];
};

uint8_t bus_buf[BUS_BUF_SIZE];
SectionBuf<UploadPacket> buffer(bus_buf, BUS_BUF_SIZE);


LCD lcd;
TinyGPSPlus gps;
HardwareSerial gps_serial(2);

enum class SwitchState {
  NotSelected,
  NoLaunch,
  AllowLaunch,
};

SwitchState switch_state = SwitchState::NotSelected;
unsigned long blink_ms;
unsigned long sent_command_ms;
unsigned long sent_location_ms;

int32_t gs_latitude;
int32_t gs_longitude;

Shared<int32_t> launcher_latitude;
Shared<int32_t> launcher_longitude;


void setup() {
  Serial.begin(115200);

  EEPROM.begin(2 + NUM_AP * (SSID_LEN + PASSWORD_LEN));

  readAP();
  
  bus.begin();
  bus.listenAll();
  bus.subscribe(launcher_latitude, 'r', 'A', LAUNCHER);
  bus.subscribe(launcher_longitude, 'r', 'O', LAUNCHER);

  gps_serial.begin(GPS_BAUD, SERIAL_8N1, GPS_RX_PIN, GPS_TX_PIN);
  Wire.begin(21, 22);

  // pinMode(21, INPUT_PULLUP);
  // pinMode(22, INPUT_PULLUP);

  pinMode(LED_PIN, OUTPUT);
  pinMode(SWITCH_PIN_1, INPUT_PULLUP);
  pinMode(SWITCH_PIN_2, INPUT_PULLUP);
  pinMode(SWITCH_PIN_3, INPUT_PULLUP);

  digitalWrite(LED_PIN, HIGH);

  lcd.begin();

  delay(1000);

  xTaskCreatePinnedToCore(loop_task, "core0", 8192, NULL, 3, &thp[0], 0);

  // digitalWrite(LED_PIN, LOW);

  lcd.setLine1("GPS Unavailable ");
  lcd.setLine2("----------------");
  lcd.show();
}

void loop() {

  setAP();

  if (WiFi.status() == WL_CONNECTED) {
    if (!wifi_connected) {
      Serial.print("WiFi connected. SSID: ");
      Serial.print(WiFi.SSID());
      Serial.print(", IP: ");
      Serial.println(WiFi.localIP());

      ntp.begin();

      char url[64];
      sprintf(url, "/api/systems/%s/packets?source=%s", system_id, source);

      if (ssl) webSocket.beginSSL(server, port, url);
      else webSocket.begin(server, port, url);

      webSocket.onEvent(webSocketEvent);
      webSocket.setReconnectInterval(5000);

      wifi_connected = true;
    }
  }
  else {
    wifi_connected = false;
  }

  if (wifi_connected) {
    webSocket.loop();
  }

  // NTP

  if (ntp.isTimeSet()) {
    unsigned long new_epoch_s = ntp.getEpochTime();
    if (new_epoch_s != epoch_s) {
      epoch_s_start_millis = millis();
      epoch_s = new_epoch_s;
    }
  }
  uint64_t epoch_ms = (uint64_t)epoch_s * 1000 + (millis() - epoch_s_start_millis);

  // Bus

  bus.update();

  if (CAN.parsePacket() > 0 && CAN.packetExtended()) {
    int dlc = CAN.packetDlc();
    uint8_t data[9];
    for (unsigned i = 0; i < dlc; i++) data[i] = CAN.read();
    CANReceived(CAN.packetId(), data, dlc);
    // Serial.printf("%d\n", dlc);
  }

  Packet packet = bus.receive();

  if (packet.isValid()) {
    if (packet.from() == FROM_LOCAL) packet.from(UNIT);
    sendViaSerial(packet);

    pushToUploadBuffer(packet);

    packet.print();
  }


  if (wifi_connected && ntp.isTimeSet() && webSocket.isConnected() && buffer.begin() != buffer.end()) {
    UploadPacket& p = (*buffer.begin()).value();
    uint64_t packet_epoch_ms = epoch_ms + p.ms - millis();
    uint8_t buf[256];
    *reinterpret_cast<uint64_t*>(buf) = packet_epoch_ms;
    unsigned len = (*buffer.begin()).size() - sizeof(UploadPacket);
    memcpy(buf + 8, p.buf, len);

    if (webSocket.sendBIN(buf, len + 8)) {
      (*buffer.begin()).free();

      digitalWrite(LED_PIN, HIGH);
      blink_ms = millis() + 10;
    }
  }

  // GPS
  while (gps_serial.available()) {
    gps.encode(gps_serial.read());
  }
  if (gps.location.isUpdated()) {
    tm t;
    time_t tim;
    t.tm_year = gps.date.year() - 1900;
    t.tm_mon  = gps.date.month() - 1;
    t.tm_mday = gps.date.day();
    t.tm_hour = gps.time.hour();
    t.tm_min  = gps.time.minute();
    t.tm_sec  = gps.time.second() + 1;
    t.tm_isdst = -1;
    tim = mktime(&t);

    long scale=10000000UL;
    gs_latitude = gps.location.rawLat().deg * scale 
                + gps.location.rawLat().billionths / 100UL;
    if (gps.location.rawLat().negative) gs_latitude = -gs_latitude;
    gs_longitude = gps.location.rawLng().deg * scale 
                 + gps.location.rawLng().billionths / 100UL;
    if (gps.location.rawLng().negative) gs_longitude = -gs_longitude;

    if (millis() > sent_location_ms + 1000 / SEND_LOCATION_FREQ) {
      uint8_t buf[BUF_SIZE(5)];
      Packet packet(buf, sizeof(buf));
      packet.set(TELEMETRY, 'P', UNIT, BROADCAST);
      packet.begin()
        .append('A', gs_latitude)
        .append('O', gs_longitude)
        .append('H', (float)gps.altitude.meters())
        .append('T', (uint32_t)tim)
        .append('S', (uint8_t)gps.satellites.value());

      bus.send(packet);
      sendViaSerial(packet);
      pushToUploadBuffer(packet);

      sent_location_ms = millis();
    }
  }
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

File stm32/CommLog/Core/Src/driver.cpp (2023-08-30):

#include "CANBus.hpp"
#include "main.h"
#include "app.h"

#define CAN_TIMEOUT_MS 10


unsigned getMillis() {
  return HAL_GetTick();
}

uint8_t EEPROMemu;

uint8_t readEEPROM(unsigned addr) { return EEPROMemu; }
void writeEEPROM(unsigned addr, uint8_t value) { EEPROMemu = value; }

unsigned getUnique() { return HAL_GetUIDw0(); }


CAN_TxHeaderTypeDef CanTxHeader;
CAN_RxHeaderTypeDef CanRxHeader;
uint32_t CanTxMailbox;

bool CANInit() {
  if (HAL_CAN_Start(&hcan) != HAL_OK) {
    Error_Handler();
  }

  if (HAL_CAN_ActivateNotification
      (&hcan, CAN_IT_RX_FIFO0_MSG_PENDING | CAN_IT_RX_FIFO1_MSG_PENDING)
      != HAL_OK) {
    Error_Handler();
  }
  CanTxHeader.RTR = CAN_RTR_DATA;
  CanTxHeader.IDE = CAN_ID_EXT;
  CanTxHeader.TransmitGlobalTime = DISABLE;
  return true;
}

bool CANSend(uint32_t ext_id, uint8_t *buf, unsigned len) {
  CanTxHeader.ExtId = ext_id;
  CanTxHeader.DLC = len;

  unsigned start = HAL_GetTick();
  while (HAL_CAN_GetTxMailboxesFreeLevel(&hcan) == 0) {
    if (HAL_GetTick() - start > CAN_TIMEOUT_MS) return false;
  }

  if (HAL_CAN_AddTxMessage(&hcan, &CanTxHeader, buf, &CanTxMailbox) != HAL_OK) {
    Error_Handler();
  }
  return true;
}

bool CANSetFilter(uint32_t id, uint32_t mask) {
  uint32_t fId = id << 3 | 0b100;
  uint32_t fMask = mask << 3 | 0b1100;

  CAN_FilterTypeDef filter0;
  filter0.FilterIdHigh = fId >> 16;
  filter0.FilterIdLow = fId;
  filter0.FilterMaskIdHigh = fMask >> 16;
  filter0.FilterMaskIdLow = fMask;
  filter0.FilterScale = CAN_FILTERSCALE_32BIT;
  filter0.FilterFIFOAssignment = CAN_FILTER_FIFO0;
  filter0.FilterBank = 0;
  filter0.FilterMode = CAN_FILTERMODE_IDMASK;
  filter0.FilterActivation = ENABLE;
  if (HAL_CAN_ConfigFilter(&hcan, &filter0) != HAL_OK) {
    Error_Handler();
  }

  CAN_FilterTypeDef filter1;
  filter1.FilterIdHigh = fId >> 16;
  filter1.FilterIdLow = fId | 0b1000;
  filter1.FilterMaskIdHigh = fMask >> 16;
  filter1.FilterMaskIdLow = fMask;
  filter1.FilterScale = CAN_FILTERSCALE_32BIT;
  filter1.FilterFIFOAssignment = CAN_FILTER_FIFO1;
  filter1.FilterBank = 2;
  filter1.FilterMode = CAN_FILTERMODE_IDMASK;
  filter1.FilterActivation = ENABLE;
  if (HAL_CAN_ConfigFilter(&hcan, &filter1) != HAL_OK) {
    Error_Handler();
  }

  return true;
}

void HAL_CAN_RxFifo0MsgPendingCallback(CAN_HandleTypeDef *hcan) {
  uint8_t data[8];
  if (HAL_CAN_GetRxMessage(hcan, CAN_RX_FIFO0, &CanRxHeader, data) !=
      HAL_OK) {
    Error_Handler();
  }

  CANReceived(CanRxHeader.ExtId, data, CanRxHeader.DLC);
}
void HAL_CAN_RxFifo1MsgPendingCallback(CAN_HandleTypeDef *hcan) {
  uint8_t data[8];
  if (HAL_CAN_GetRxMessage(hcan, CAN_RX_FIFO1, &CanRxHeader, data) !=
      HAL_OK) {
    Error_Handler();
  }

  CANReceived(CanRxHeader.ExtId, data, CanRxHeader.DLC);
}

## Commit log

2019-10-18 Create igniter driver
    [IgniterDriver.brd, IgniterDriver.sch]
2019-10-26 Add battery power board
    [BatteryPower.brd, BatteryPower.sch]
2019-10-26 Add USB&LiPo power board
    [USB&LiPoPower.brd, USB&LiPoPower.sch]
2019-10-26 Add igniter driver board
    [IgniterDriver.brd, IgniterDriver.sch]
2019-11-01 Add communication and logging board
    [Comm&Log.brd, Comm&Log.sch]
2019-11-02 Add base board
    [BaseBoard.brd, BaseBoard.sch]
2019-11-05 Layout battery power board
    [BatteryPower.brd, BatteryPower.sch]
2019-11-06 Layout and route base board
    [BaseBoard.brd, BaseBoard.sch]
2019-11-07 Layout igniter driver board
    [IgniterDriver.brd, IgniterDriver.sch]
2019-11-10 Layout USB and LiPo power board
    [USB&LiPoPower.brd, USB&LiPoPower.sch]
2019-11-11 Add sensing and GPIO board
    [sensing.brd, sensing.sch]
2019-11-11 Complete base board
    [BaseBoard.brd, BaseBoard.sch]
2019-11-12 Complete USB & LiPo power board
    [USB&LiPoPower.brd, USB&LiPoPower.sch]
2019-11-12 Complete battery power board
    [BatteryPower.brd, BatteryPower.sch]
2019-11-12 Complete igniter driver board
    [IgniterDriver.brd, IgniterDriver.sch]
2019-11-12 Complete communication & logging board
    [Comm&Log.brd, Comm&Log.sch]
2019-11-13 Clean silk print
    [BaseBoard.brd, BatteryPower.brd, Comm&Log.brd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]
2020-05-11 Some fixes
    [BaseBoard.brd, Comm&Log.brd, Comm&Log.sch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]
2020-05-11 Add stm32 project of Comm&Log module
    [CommLog Debug.cfg]
2020-05-11 Add stm32 project of BatteryPower module
2021-04-17 Add spin gantry launcher
    [BaseBoardv2.brd, BaseBoardv2.sch, BatteryPower Debug.cfg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]
2022-06-23 Add BMX055
    [CommLog Debug.cfg, IMU Debug.cfg]
2022-06-26 Add pressure sensor, voltage and current sensing
    [BatteryPower Release.cfg, IMU Release.cfg]
2022-07-03 Add nav board
    [Nav.brd, Nav.sch]
2022-08-12 Update CAN command channel
    [Comm&Log.sch]
2022-08-22 Add nav module
    [Nav Debug (1).cfg, Nav Debug.cfg, Nav Release.cfg]
2022-08-22 Fix reset wire
    [Nav.brd, Nav.sch]
2022-08-22 Add writing log to SD card
    [CommLog Release.cfg]
2022-08-24 Add ground station lcd controller
2022-09-09 Update GS server
    [GSServer.sch]
2022-09-10 Use sync web server (not working)
    [GSServer.ino, LCD.cpp]
2022-09-11 Fix bug and add chart
    [GSServer.ino]
2022-09-12 Fix command decoding bug
    [GSServer.ino]
2022-09-12 Add navigation module
    [Nav Debug.cfg, Nav Release.cfg]
2022-09-13 Add IMU module
    [CommLog Debug.cfg, IMU Debug.cfg, IMU Release.cfg]
2022-09-13 Add sensor module
    [Sensor Debug.cfg, Sensor Release.cfg]
2022-09-16 Add igniter module
    [Igniter Debug.cfg, Igniter Release.cfg]
2023-05-07 新モジュール回路設計完了
    [BatteryPowerV2.brd, BatteryPowerV2.sch, INS.brd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]
2023-05-24 LoRaモジュール、基板設計完了です。
    [LoRa.brd]
2023-05-25 BatteryPowerV2とINSの基板設計です。変えたつもりはないんですけど、schの方が変わっちゃってる可能性があって、申し訳ないんですけど確認お願いします。
    [BatteryPowerV2.brd, BatteryPowerV2.sch, INS.brd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]
2023-05-27 RCSモジュール追加
    [RCS.brd, RCS.sch]
2023-05-27 新モジュールの雛形
    [BatteryPower Debug.cfg, BatteryPower Release.cfg, CommLog Debug.cfg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]
2023-05-27 一旦保存
2023-05-27 RCS基板を追加
    [RCS.brd, RCS.sch]
2023-05-27 修正途中
    [BatteryPowerV2.brd, BatteryPowerV2.sch, LoRa.brd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]
2023-06-07 大変お待たせしました。BatteryPowerV2とINSの改良版です。確認お願いします。
    [BatteryPowerV2.brd, INS.brd]
2023-06-07 気圧センサ用ポートを追加
    [RCS.brd, RCS.sch]
2023-08-16 モジュールの説明を追加
2023-08-18 新LoRaモジュールのファームウェアを追加(WIP)
    [CommLog Release.cfg, LoRa Debug.cfg]
2023-08-30 Battery Power v2 完成
    [BatteryPowerV2 Debug.cfg, BatteryPowerV2 Release.cfg, BatteryPowerV2.cfg]
2023-08-31 ADC DMA修正
2023-08-31 デバッグ用USBシリアルモジュール
    [USBLiPoPower Release.cfg]
2023-09-08 Comm&Logモジュール最新版
    [CommLog Debug.cfg, CommLog Release.cfg]

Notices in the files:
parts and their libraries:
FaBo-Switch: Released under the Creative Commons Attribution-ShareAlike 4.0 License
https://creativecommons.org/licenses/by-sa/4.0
